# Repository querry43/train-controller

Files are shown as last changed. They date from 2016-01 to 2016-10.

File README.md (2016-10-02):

Whistle Board
=============
The Whistle Board is a an inexpensive and easily assembled kit for controlling your model trains with a microcontroller.

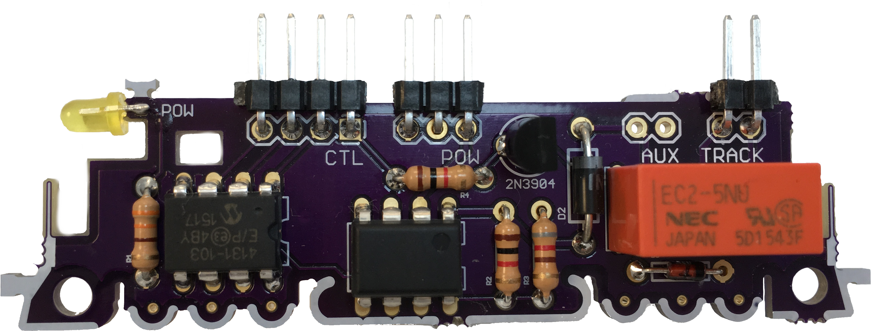
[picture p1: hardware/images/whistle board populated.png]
Completed Kit


Specifications
--------------
 * Supports N and Z scales
 * Control multiple trains with multiple boards
 * Works with your existing train hardware
 * Does not require any modifications to trains or track
 * Does not use PWM which can overheat small motors
 * 700mA per channel
 * Supports both 5V and 3.3V logic

Whistle Board Parts List
------------------------
https://docs.google.com/spreadsheets/d/1KjXTjjhD9g_6WGJ1dTABSkwde-gAP-HaPDzFgPxGlLw/edit#gid=0

Total Cost: ~ $12
 
Output voltage
--------------
This board can be assembled for different model scales by adjusting the value of R3.  Be sure to select the correct value for your scale or you risk damaging your engines.

*Output Voltage Table*

| Scale | Max Output Voltage | R3 |
|---|---|---|
| Z |  8V | 1.6k ohm |
| N | 12V | 820  ohm |

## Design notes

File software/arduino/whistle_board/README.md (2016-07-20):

Whistle Board Arduino Software
==============================
Control a Whistle Board from an Arduino or Arduino compatible by sending and receiving commands serially.

Serial commands
---------------
    ? - This help dialog
    GO index speed - Go at given speed, -100 to 100
    STOP index - Slow to speed 0
    HALT index - Immediate halt

These commands are case insensitive and can be abbreviated down to a single character.  For example: "g 0 100".  Commands are separated by newlines and/or carriage returns.  Each command takes an optional index.  This is the train line number when controlling multiple trains, starting at 0.  If an index is not given, 0 is assumed.

Serial Responses
----------------

When the Arduino is ready, it will send the message "READY".  After that, it will respond to all commands either with "OK: <message>" or "NOT OK: <message>" where the message will usually include the command it is responding to.  In addition to responses, the arduino may respond with additional status information:

    OK: ACCEL index value - The current speed values when accelerating to a requested speed

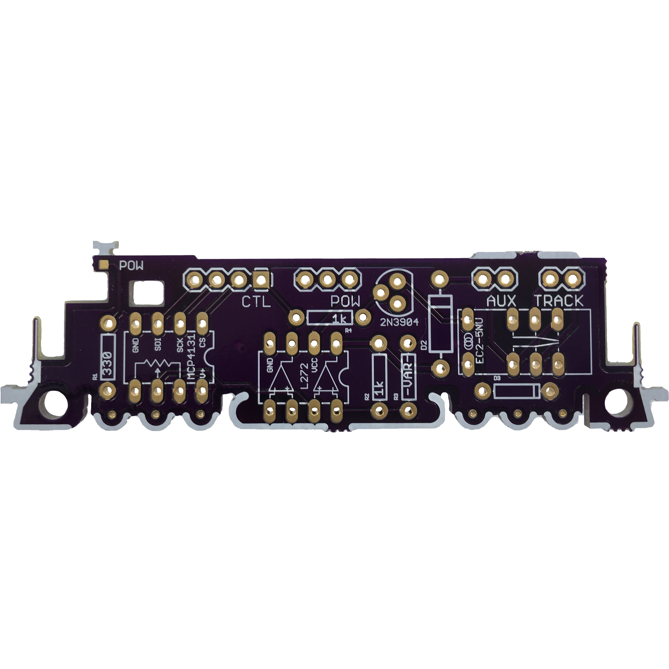
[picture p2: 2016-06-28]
hardware/images/whistle board square.png

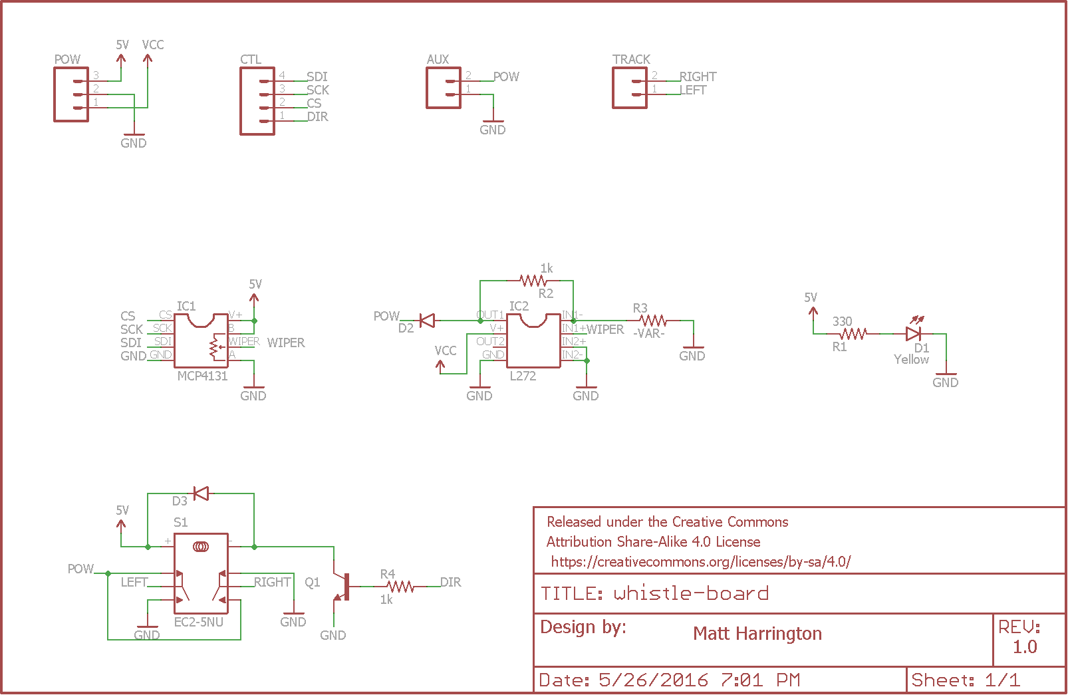
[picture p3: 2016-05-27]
hardware/images/whistle-board schematic.png

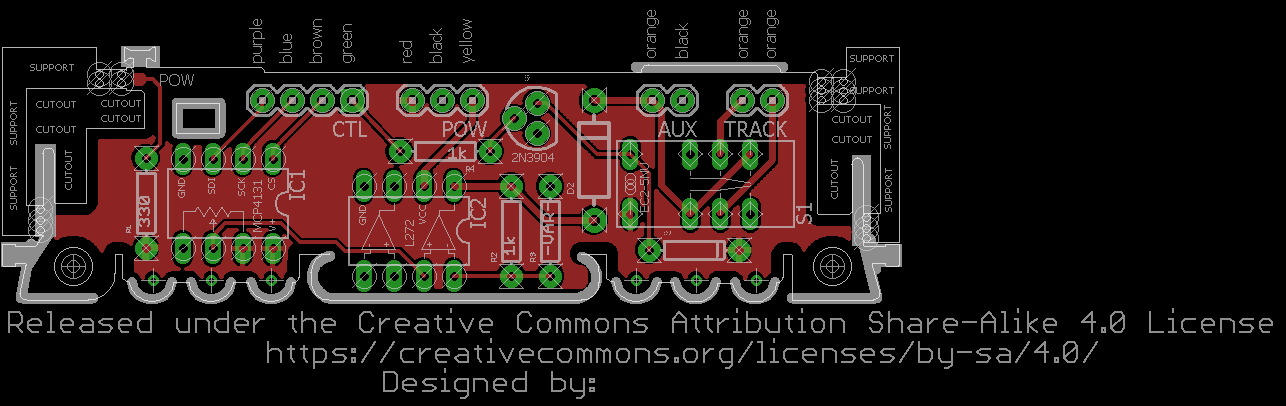
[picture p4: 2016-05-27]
hardware/images/whistle-board top.png

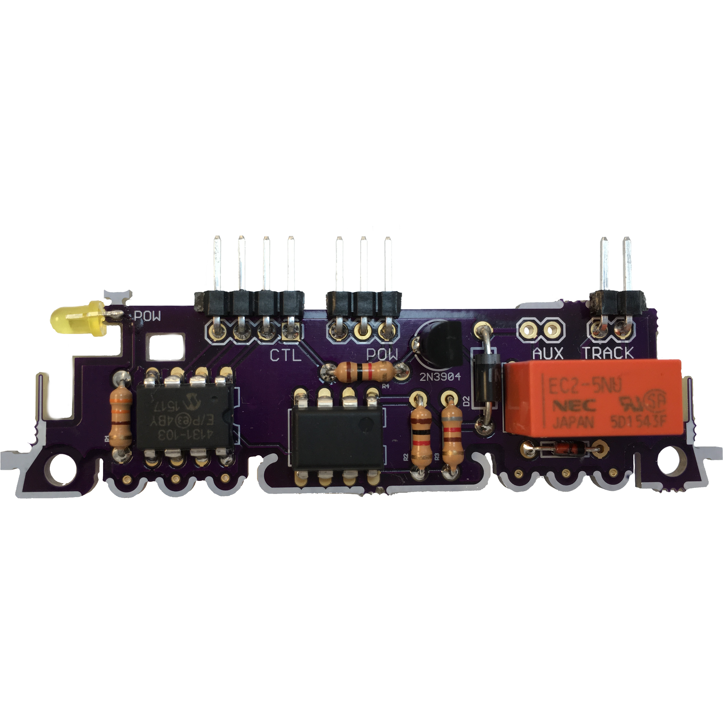
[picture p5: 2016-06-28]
hardware/images/whistle board populated square.png

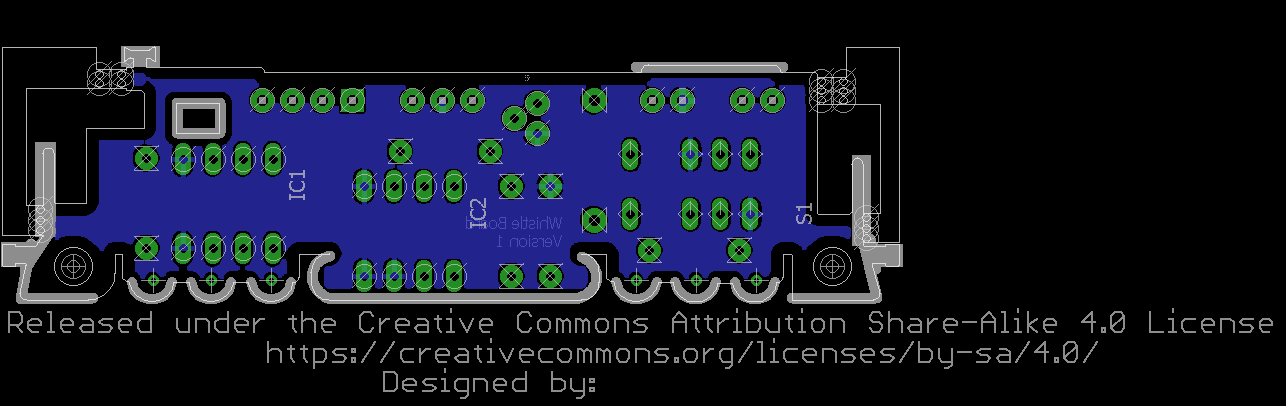
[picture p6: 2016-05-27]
hardware/images/whistle-board bottom.png

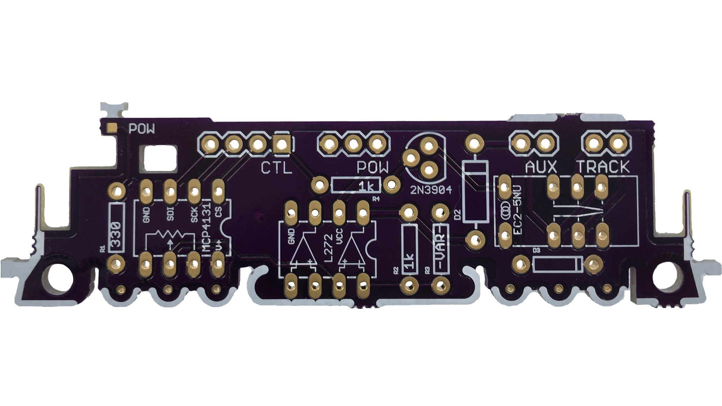
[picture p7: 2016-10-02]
hardware/images/whistle board kickstart.png

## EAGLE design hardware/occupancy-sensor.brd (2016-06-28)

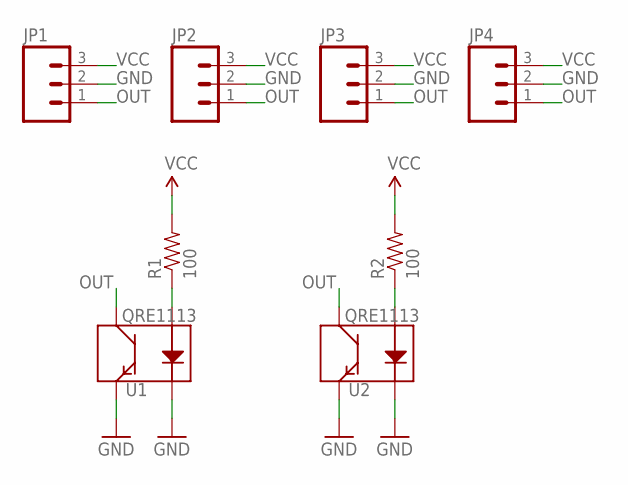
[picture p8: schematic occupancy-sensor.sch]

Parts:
JP1, JP2, JP3, JP4: M031X03_NO_SILK; 1X03_NO_SILK
R1, R2: 100; 0603-RES
U1, U2: QRE1113; QRE1113-W

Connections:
GND: JP1.2, JP2.2, JP3.2, JP4.2, U1.2 (K), U1.4 (E), U2.2 (K), U2.4 (E)
unnamed: R1.1, U1.1 (A)
unnamed: R2.1, U2.1 (A)
OUT: JP1.1, JP2.1, JP3.1, JP4.1, U1.3 (C), U2.3 (C)
VCC: JP1.3, JP2.3, JP3.3, JP4.3, R1.2, R2.2

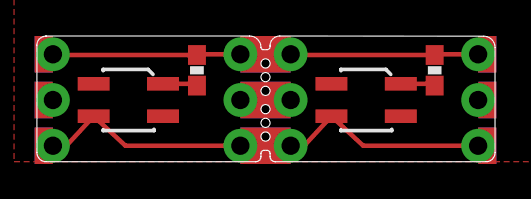
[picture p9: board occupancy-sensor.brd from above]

Board: 2 copper layers, 25.5 x 7.0 mm, 8 parts (0 on the bottom side), 5 nets.

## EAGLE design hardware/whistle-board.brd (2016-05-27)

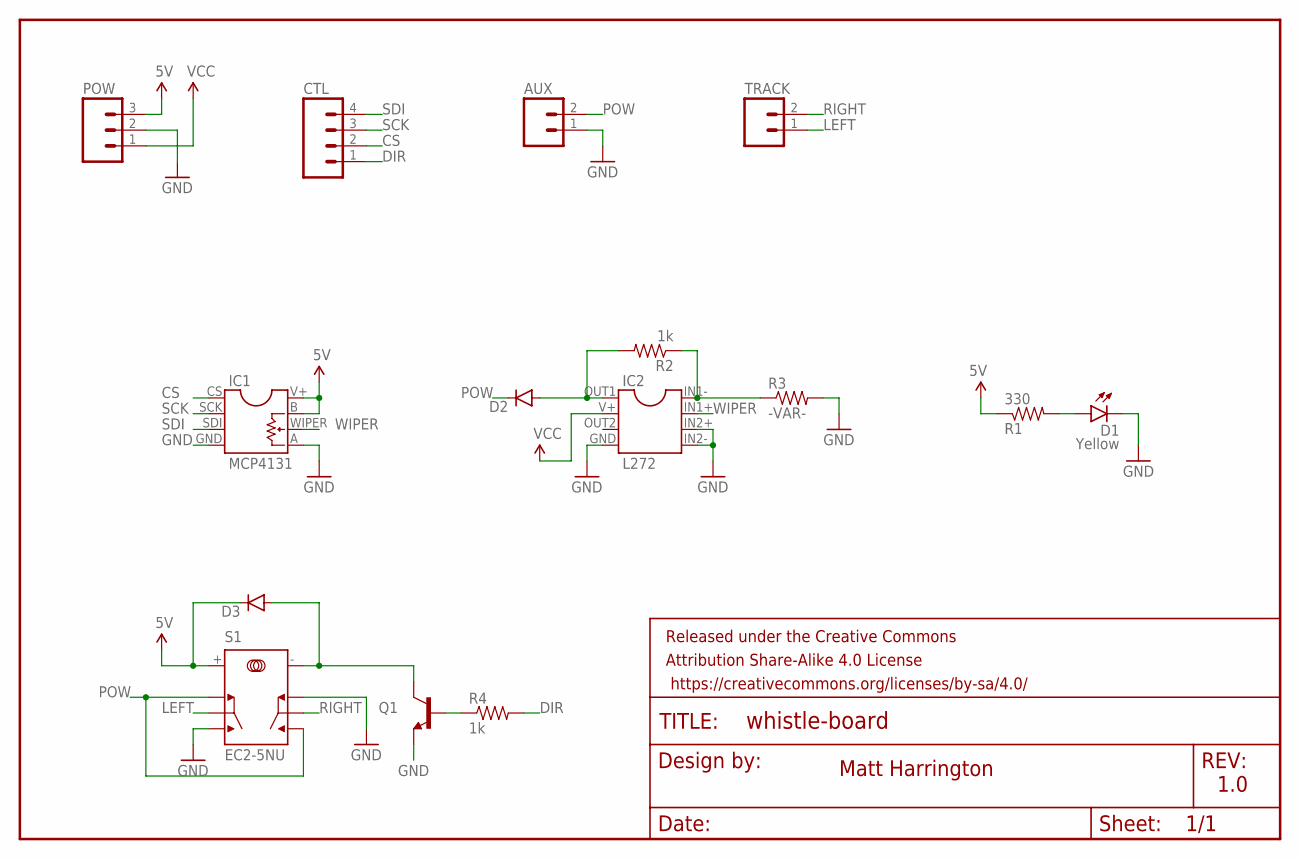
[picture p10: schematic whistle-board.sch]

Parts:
AUX: M02PTH; 1X02
CTL: M04PTH; 1X04
D1: Yellow; LED-EDGE
D2: DIODEPTH; DIODE-1N4001
D3: DIODE1N4148; DIODE-1N4148
FRAME1: FRAME-LETTER; CREATIVE_COMMONS
IC1: MCP4131
IC2: L272
POW: M03PTH; 1X03
Q1: TRANSISTOR_NPNTO92; TO-92
R1: 330; AXIAL-0.3
R2, R4: 1k; AXIAL-0.3
R3: -VAR-; AXIAL-0.3
S1: EC2-5NU
TRACK: M02PTH; 1X02

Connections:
5V: D3.C, IC1.B, IC1.V+, POW.3, R1.P$1 (1), S1.+
CS: CTL.2, IC1.CS
DIR: CTL.1, R4.P$2 (2)
GND: AUX.1, D1.C, IC1.A, IC1.GND, IC2.GND, IC2.IN2+, IC2.IN2-, POW.2, Q1.1 (E), R3.P$2 (2), S1.NC2, S1.NO1
LEFT: S1.COM1, TRACK.1
unnamed: D3.A, Q1.3 (C), S1.-
unnamed: Q1.2 (B), R4.P$1 (1)
unnamed: IC2.IN1-, R2.P$1 (1), R3.P$1 (1)
unnamed: D2.A, IC2.OUT1, R2.P$2 (2)
unnamed: D1.A, R1.P$2 (2)
POW: AUX.2, D2.C, S1.NC1, S1.NO2
RIGHT: S1.COM2, TRACK.2
SCK: CTL.3, IC1.SCK
SDI: CTL.4, IC1.SDI
VCC: IC2.V+, POW.1
WIPER: IC1.WIPER, IC2.IN1+

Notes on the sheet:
Matt Harrington
1.0

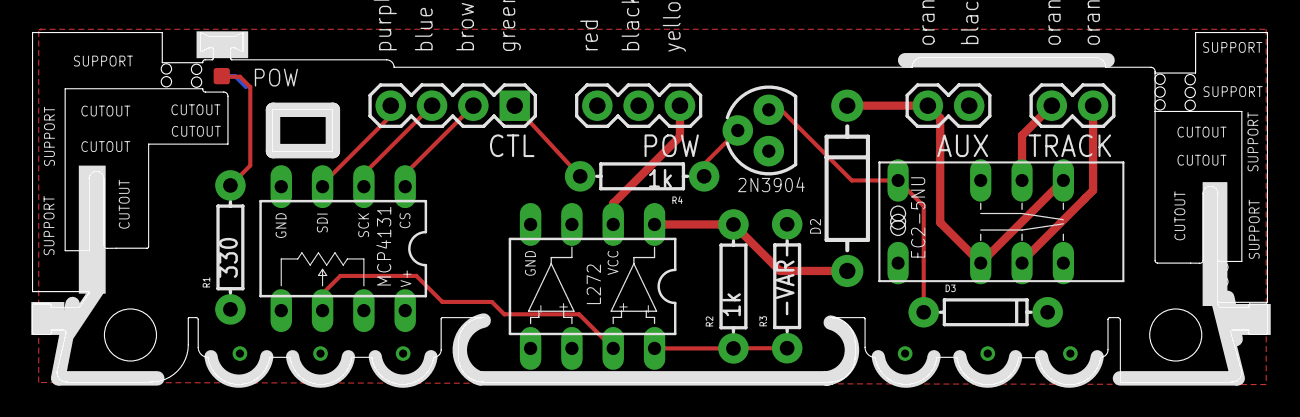
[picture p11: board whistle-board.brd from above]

Board: 2 copper layers, 75.9 x 21.7 mm, 16 parts (1 on the bottom side), 16 nets.

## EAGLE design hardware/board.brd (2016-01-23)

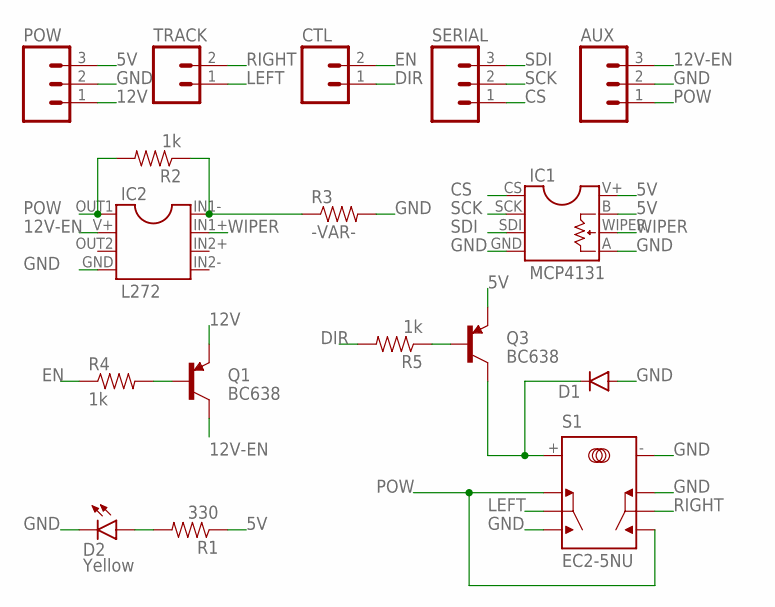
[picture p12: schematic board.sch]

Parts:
AUX: M03PTH; 1X03
CTL: M02PTH; 1X02
D1: DIODE1N4148; DIODE-1N4148
D2: Yellow; LED-EDGE
IC1: MCP4131
IC2: L272
POW: M03PTH; 1X03
Q1, Q3: BC638; TO-92
R1: 330; AXIAL-0.3
R2, R4, R5: 1k; AXIAL-0.3
R3: -VAR-; AXIAL-0.3
S1: EC2-5NU
SERIAL: M03PTH; 1X03
TRACK: M02PTH; 1X02

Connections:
5V: IC1.B, IC1.V+, POW.3, Q3.1 (E), R1.P$1 (1)
12V: POW.1, Q1.1 (E)
12V-EN: AUX.3, IC2.V+, Q1.3 (C)
CS: IC1.CS, SERIAL.1
DIR: CTL.1, R5.P$2 (2)
EN: CTL.2, R4.P$1 (1)
GND: AUX.2, D1.A, D2.C, IC1.A, IC1.GND, IC2.GND, POW.2, R3.P$2 (2), S1.-, S1.NC2, S1.NO1
LEFT: S1.COM1, TRACK.1
unnamed: Q1.2 (B), R4.P$2 (2)
unnamed: D1.C, Q3.3 (C), S1.+
unnamed: IC2.IN1-, R2.P$1 (1), R3.P$1 (1)
unnamed: Q3.2 (B), R5.P$1 (1)
unnamed: D2.A, R1.P$2 (2)
POW: AUX.1, IC2.OUT1, R2.P$2 (2), S1.NC1, S1.NO2
RIGHT: S1.COM2, TRACK.2
SCK: IC1.SCK, SERIAL.2
SDI: IC1.SDI, SERIAL.3
WIPER: IC1.WIPER, IC2.IN1+

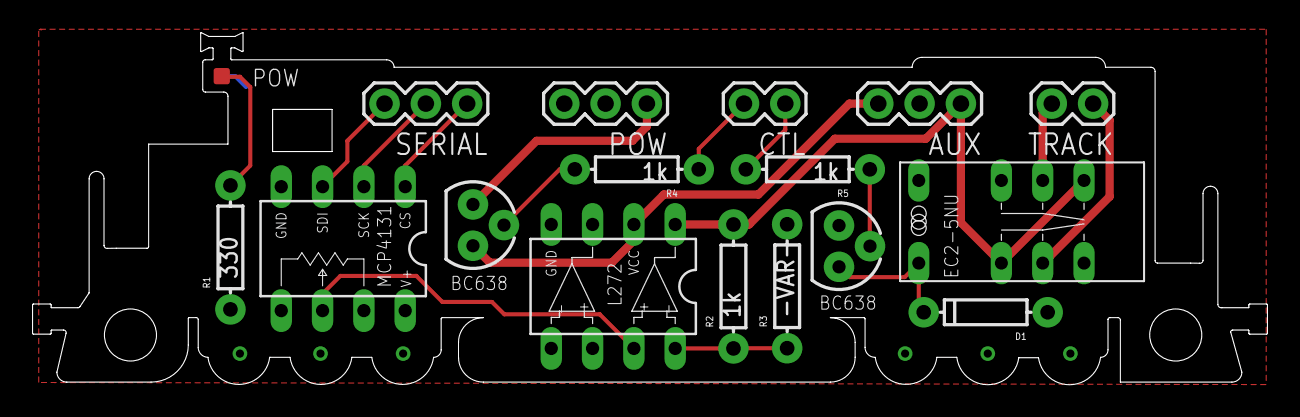
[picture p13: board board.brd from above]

Board: 2 copper layers, 75.9 x 21.7 mm, 17 parts (1 on the bottom side), 18 nets.

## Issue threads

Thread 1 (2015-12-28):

3.3v support

querry43, 2015-12-28:
MCs with wireless or bluetooth frequently run at 3.3v.  It is not clear what would be required to make this board support both 3.3v and 5v.

The mcp4131 and opamps should work although it would require different opamp resistors.

The relay may be a problem.  The Farnell datasheet states the 5v relay will switch with 3.75v at the least and the nec-tokin datasheet states that the max coil voltage cannot exceed 1.5 times the nominal voltage.

One option is to switch the relay off V+ and use a current-limiting resistor which would vary based on V+.  Another option is to offer 3v and 5v variants.

Closed 2016-01-16.

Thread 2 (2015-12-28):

no board labeling

querry43, 2015-12-28:
There is no version, copyright, or other information silkscreened on the board.

querry43, 2016-01-17:
added a place for branding when ready

Closed 2016-01-17.

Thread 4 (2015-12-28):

consider swapping the 2n2222 for another BCD638 to simplify assembly

querry43, 2015-12-28:

Closed 2016-01-16.

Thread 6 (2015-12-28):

what is the total price and what can be done to bring it down?

querry43, 2015-12-28:

querry43, 2015-12-28:
pcb: 12.75 / 3
supply: 6 (https://www.sparkfun.com/products/9442)
resistors and leds: negligible
BCD638: 0.3
2n2222: ? (non-stock item)
L272: 0.6
EC2-5NU: 1.6
MCP4131: 0.7

~ 13.50$

31% is the pcb
45% is the supply

querry43, 2016-01-18:
Consider removing the m(i) and m(v) headers.  These can be measured as input current and as rectified output voltage.  This will remove the cost of 2 headers and reduce crowding.

querry43, 2016-01-19:
Buy male connectors from digikey and female with wires from sparkfun. This also gives access to blue/black cables.

querry43, 2016-01-21:
Molex KK cabling is about 1$ cheaper but will require some additional assembly (pin crimping).  I think that might be a better way to go because it simplified the design and makes it more flexible and accessible.

Closed 2016-02-20.

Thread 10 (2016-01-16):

could a dac replace the digipot?

querry43, 2016-01-16:
MCP4801 would have a simpler schematic with similar footprint and control but at greater price.

querry43, 2016-01-16:
This would make sense if it could replace additional components but that does not appear to be the case.

Closed 2016-01-16.

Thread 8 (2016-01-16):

what about a dedicated regulator board?

querry43, 2016-01-16:
one board would supply power to multiple controllers and MCs

dropping ~20v down to 5 can be tricky, consider lm2596

querry43, 2016-01-16:
Maybe this would be a rectifier that used a train transformer as input and  a 5v wall wort.

querry43, 2016-01-17:
Inputs
------
5v via barrel jack
v+ from transformer via screw terminals

Outputs
-------
gnd, 5v, v+ via solder pads to controller
gnd, 5v via jst to mc

Board components
----------------
bridge rectifier for v+
power led for 5v
power led for v+

Closed 2016-01-17.

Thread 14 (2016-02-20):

is it a problem that the controller idles at 0.18v?

querry43, 2016-02-20:

Closed 2016-05-27.

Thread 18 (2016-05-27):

Occupancy sensor needs rounded corners and additional parting perforations

querry43, 2016-05-27:

querry43, 2016-06-21:
* Rounded corners
* Labels
* More perforations
* Larger pads on sensor
* Check resistor wattage

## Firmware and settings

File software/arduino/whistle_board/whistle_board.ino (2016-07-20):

#include <SPI.h>
#include <McpDigitalPot.h>

const uint8_t maxbuflen = 16;
const int8_t acceleration = 2;

class WhistleBoard {
public:
  WhistleBoard(const uint8_t ss, const uint8_t dir, const uint8_t index) : _speed(0), _target_speed(0), _dir(dir), _index(index), _digital_pot(ss, 10000) {
    pinMode(_dir, OUTPUT);
  }

  void set_target_speed(int8_t target_speed) { _target_speed = target_speed; }

  void halt() {
    _speed = 0;
    _target_speed = 0;
    _update_digipot();
  }

  void update() {
    if (_speed > _target_speed) {
      _speed = max(_speed - acceleration, _target_speed);
      _update_digipot();
    } else if (_speed < _target_speed) {
      _speed = min(_speed + acceleration, _target_speed);
      _update_digipot();
    }
  }
 
private:
  int8_t _speed, _target_speed;
  uint8_t _dir, _index;
  McpDigitalPot _digital_pot;

  WhistleBoard();

  void _update_digipot() {
    if (_speed >= 0) digitalWrite(_dir, LOW);
    else             digitalWrite(_dir, HIGH);

    _digital_pot.setResistance(0, map(abs(_speed), 0, 100, 10000, 0));

    Serial.print("OK: ACCEL ");
    Serial.print(_index);
    Serial.print(" ");
    Serial.println(_speed);
    delay(100);
  }
};

WhistleBoard wbs[] = {
  WhistleBoard(8, 9, 0),
  WhistleBoard(6, 7, 1),
};

void setup() {
  SPI.begin();

  Serial.begin(9600);
  Serial.println("READY");
}

void loop() {
  char command[maxbuflen];
  if (read_command(command)) {
    run_command(command);
  }

  wbs[0].update();
  wbs[1].update();
}

bool read_command(char* command) {
  static char buf[maxbuflen];
  static uint8_t buflen = 0;

  if (Serial.available()) {
    char byte = Serial.read();

    // newline
    if (byte == '\n' || byte == '\r') {
      if (buflen > 0) {
        buf[buflen] = 0;
        strncpy(command, buf, buflen+1);
        buflen = 0;
        return true;
      } else {
        return false;
      }

    // overflow
    } else if (buflen == maxbuflen-1) {
      buflen = 0;

    // chars
    } else {
      buf[buflen++] = byte;
    }

    return false;
  }
}

void run_command(char* line) {

  char command_str[maxbuflen],
    tok1_str[maxbuflen],
    tok2_str[maxbuflen];

  strncpy(command_str, strtok(line, " "), maxbuflen-1);
  strncpy(tok1_str, strtok(NULL, " "), maxbuflen-1);
  strncpy(tok2_str, strtok(NULL, " "), maxbuflen-1);

  char command_chr = tolower(command_str[0]);
  int32_t tok1_int = strtol(tok1_str, NULL, 10);
  int32_t tok2_int = strtol(tok2_str, NULL, 10);

  Serial.print("COMMAND: ");
  Serial.print(command_str);
  Serial.print(", TOK1: ");
  Serial.print(tok1_str);
  Serial.print(", TOK2: ");
  Serial.println(tok2_str);

  switch (command_chr) {
    case '?':
      Serial.println("? - This help dialog");
      Serial.println("GO index speed - Go at given speed, -100 to 100");
      Serial.println("STOP index - Slow to 0 speed");
      Serial.println("HALT index - Immediate halt");
      Serial.println();
      Serial.println("Commands are case insensitive and can be abbreviated to single characters");
      Serial.println("In all commands, index is optional and defaults to 0");
      break;

    case 'g':
      // 0 parameters
      if (strlen(tok1_str) == 0) {
        Serial.println("NOT OK: GO Missing parameters");
        break;
      // 1 parameter
      } else if (strlen(tok2_str) == 0) {
        tok2_int = tok1_int;
        tok1_int = 0;
      }

      if (tok1_int < 0 || tok1_int >= 2) {
        Serial.println("NOT OK: GO Index out of range");
      } else if (tok2_int < -100 || tok2_int > 100) {
        Serial.println("NOT OK: GO Value out of range");
      } else {
        wbs[tok1_int].set_target_speed(tok2_int);
        Serial.print("OK: GO ");
        Serial.print(tok1_int);
        Serial.print(" ");
        Serial.println(tok2_int);
      }

      break;

    case 's':
      // 0 parameters
      if (strlen(tok1_str) == 0)
        tok1_int = 0;

      if (tok1_int < 0 || tok1_int >= 2) {
        Serial.println("NOT OK: STOP Index out of range");
      } else {
        wbs[tok1_int].set_target_speed(0);
        Serial.print("OK: STOP ");
        Serial.println(tok1_int);
      }
      break;

    case 'h':
      // 0 parameters
      if (strlen(tok1_str) == 0)
        tok1_int = 0;

      if (tok1_int < 0 || tok1_int >= 2) {
        Serial.println("NOT OK: HALT Index out of range");
      } else {
        wbs[tok1_int].halt();
        Serial.print("OK: HALT ");
        Serial.println(tok1_int);
      }
      break;

    default:
      Serial.print("NOT OK: Unknown command: ");
      Serial.println(command_str);
      break;
  }
}

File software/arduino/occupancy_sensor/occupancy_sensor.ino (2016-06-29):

const uint8_t led_pin = 13;
const uint8_t enable_pin = 9;
const uint8_t signal_pin = A0;

const uint16_t threshold = 60;
const uint16_t transition_time = 10;

void setup() {
  _setup_sensor();
}

void loop() {
  _read_sensor();
}

void _setup_sensor() {

  pinMode(enable_pin, OUTPUT);
  pinMode(led_pin, OUTPUT);
  pinMode(signal_pin, INPUT_PULLUP);

  digitalWrite(enable_pin, HIGH);
  digitalWrite(led_pin, LOW);
  digitalWrite(signal_pin, HIGH);

  Serial.begin(9600);
}

void _read_sensor() {
  const int16_t r1 = analogRead(signal_pin);

  digitalWrite(enable_pin, LOW);
  delay(transition_time);

  const int16_t r2 = analogRead(signal_pin);

  digitalWrite(enable_pin, HIGH);
  delay(transition_time);

  const int16_t r3 = analogRead(signal_pin);

  digitalWrite(led_pin, max(abs(r1 - r2), abs(r3 - r2)) > threshold);

  //Serial.print(r1); Serial.print("\t"); Serial.print(r2); Serial.print("\t"); Serial.println(r3);
  //delay(1000);
}

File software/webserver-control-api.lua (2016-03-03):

dofile('mcp4131.lua')

TrainControl = {}

TrainControl[0] = MCP4131:new({cs = 8, dir_pin = 3})
TrainControl[1] = MCP4131:new({cs = 2, dir_pin = 0})

num_train_lines = 2

for i=0,num_train_lines-1 do
  TrainControl[i]:set(0)
  TrainControl[i].val = 0
  gpio.mode(TrainControl[i].dir_pin, gpio.OUTPUT)
  gpio.write(TrainControl[i].dir_pin, gpio.LOW)
end

return function (path, query)
  local response = ''

  for i=0,num_train_lines-1 do
    local s = query['speed[' .. i .. ']']
    if(s) then
      local si = tonumber(s)
      TrainControl[i]:set(100 - math.abs(si))
      TrainControl[i].val = si
    end

    if(i>0) then response = response .. ',' end

    response = response .. TrainControl[i].val
  end

  return 200, '{"num_train_lines":' .. num_train_lines ..',"speed":[' .. response .. ']}'
end

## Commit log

2015-10-28 fixing digipot wiring
    [train-controller.brd]
2015-12-28 board v2, adding readme and license
    [train-controller.brd, train-controller.sch]
2016-01-16 addressing several items from the bug/feature list
    [train-controller.brd, train-controller.sch]
2016-01-17 adding controller board
    [supply.brd, supply.sch, train-controller.brd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]
2016-01-21 getting close to final v2 board, swapping out connectors for molex kk
    [train-controller.brd, train-controller.sch]
2016-01-22 update version and documentation
    [supply.brd, supply.sch, train-controller.sch]
2016-01-23 organizing, adding lua tools
    [supply.brd, supply.sch, train-controller.brd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]
2016-01-23 renaming things, adding images
    [board.brd, board.sch, supply.brd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]
2016-01-27 working on a different distribution board
    [feather-board.brd, feather-board.sch]
2016-01-31 reducing memory footprint
2016-02-21 revisions after the most recent draft was assembled and tested
    [feather-board.brd, feather-board.sch, supply.brd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]
2016-02-21 sloppily terminating unused opamp
    [whistle-board.brd, whistle-board.sch]
2016-04-15 adding/fixing diodes, adding silkscreen details
    [whistle-board.brd, whistle-board.sch]
2016-04-24 0.1 pin spacing
    [whistle-board.brd]
2016-04-27 changes after last fab
    - removing opamp short to ground
    - fixing missing silkscreen details
    - small component moves
    - adding support around left railing
    [whistle-board.brd]
2016-05-08 Adding support and ordering (v3)
    [whistle-board.brd]
2016-05-08 begin work on occupancy sensor
    [occupancy-sensor.brd, occupancy-sensor.sch]
2016-05-27 superficial labeling update
    [whistle-board.brd]
2016-05-27 Updating license, annotating schematic, updating images, moving software
    [whistle-board.brd, whistle-board.sch]
2016-06-07 updated arduino software for new board (no enable)
2016-06-27 arduino support for multiple lines
2016-06-28 occupancy sensor improvements
    * rounded corners
    * labels
    * larger pads
    * more perforations
    [occupancy-sensor.brd, occupancy-sensor.sch]
2016-06-29 adding occupancy sensor software, organizing
2016-07-20 updating arduino software, making commands easier and more explicit

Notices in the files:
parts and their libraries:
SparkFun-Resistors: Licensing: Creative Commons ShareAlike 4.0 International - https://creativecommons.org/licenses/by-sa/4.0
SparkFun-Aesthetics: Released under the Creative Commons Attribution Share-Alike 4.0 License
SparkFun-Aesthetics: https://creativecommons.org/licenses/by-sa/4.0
